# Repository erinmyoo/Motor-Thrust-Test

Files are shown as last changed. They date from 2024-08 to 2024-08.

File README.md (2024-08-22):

NSF REU: Collaborative Human-Robot Interaction for Robots in the Field at University of Nevada, Reno

For information about the full research project: [Paper](https://github.com/erinmyoo/Motor-Thrust-Test/blob/main/REU_Erin_Yoo.pdf)

# Motor-Thrust-Test
The goal of the Motor Thrust Test is to determine the reliability of the motors chosen for a solar-powered UAV called the Gannet. Wind Tunnel and Cyclic Marine Testing will evaluate the performace of the motor-propeller combination that is reported to produce 0.8 kg of thrust at a speed of 14 m/s and cruise power of 110 W.

## Test Stand Design
Completed Solidworks CAD Assembly and BOM is uploaded
* CAD Assembly is named ZBarStand

Manufacturing methods: horizontal bandsaw, mill, CNC mill (for Motor Mount)

Important Features:
* Motor Mount: Machined aluminum, cross mounting pattern to fit motors from 19 mm to 25 mm
* Single-Point Load Cell: withstand up to 10 kg of pressure
* Z-bar Configuration: accounts for the lip of the test tank, COG allows for the motor to fall back into the tank when disengaged
* Base Angle Brackets: bearings to allow the Z-bar to rotate, slots on top for hardstops
* Hardstops: two slots to press fit into Base Angle Brackets to contrain movement
* Pitot Tube: measures air speed and ground speed, not included in CAD



## Wind Tunnel Testing - Dynamic Thrust 
Dynamic thrust testing will conduct a Wind Tunnel Test using various motor and propeller combinations. The Test Stand will be strapped on top of the car while driving at the Gannet's cruise speed of 14 m/s. 

Status:
* Script finished
* Tested once
* Needs further data/testing to determine if motor efficiency is consistently calculated to be ~37%

## Cyclic Marine Testing - Static Thrust
Static thrust of the motor will be evaluated through Cyclic Marine Testing that simulates a multi-day mission at sea to validate corrosion mitigation. The motor will run continuously for 24 hours while the Test Stand dunks the motor in and out of the test tank filled with salt water.

Status:
* Script is mostly finished - issues with system receiving motor commands
* Testing needs to start

## Test Script
Python, ROS and MAVROS was used to automate testing and log data to a csv file.

Libraries used for setting up the Load Cell:
* [smbus2](https://pypi.org/project/smbus2/)
* [PyNAU7802](https://github.com/BrunoB81HK/PyNAU7802/tree/main)

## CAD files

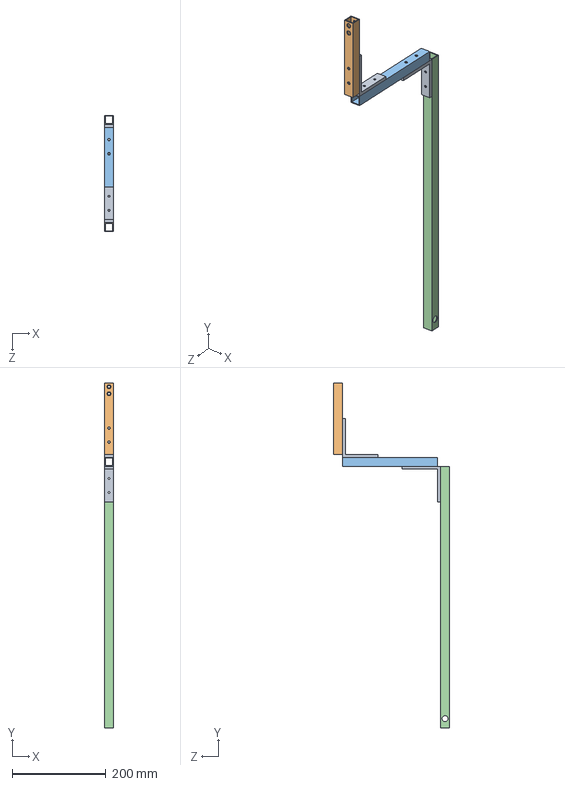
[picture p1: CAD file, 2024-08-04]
Test Stand CAD Files/ZBar.SLDASM
19.1 x 736.6 x 247.7 mm
Tube3
Tube2
Tube1
ZBarBracket x 2

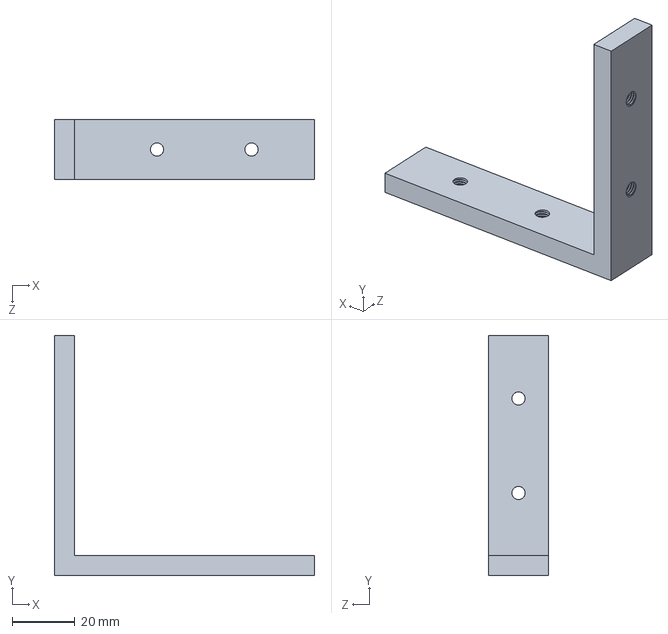
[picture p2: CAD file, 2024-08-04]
Test Stand CAD Files/ZBarBracket.SLDPRT
82.6 x 76.2 x 19.1 mm

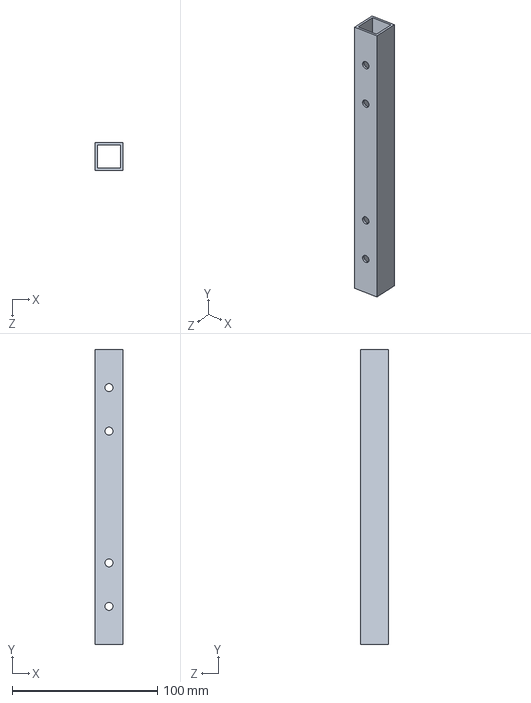
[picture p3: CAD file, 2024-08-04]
Test Stand CAD Files/Tube2.SLDPRT
19.1 x 203.2 x 19.1 mm

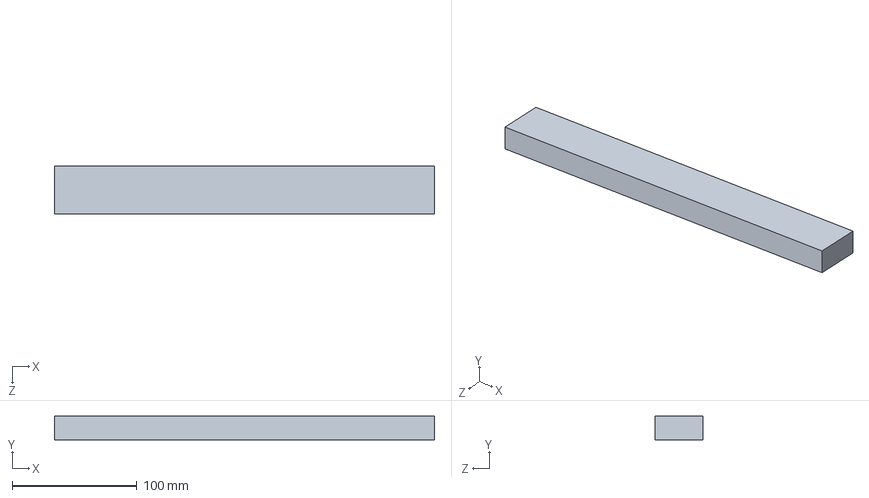
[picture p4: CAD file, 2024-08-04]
Test Stand CAD Files/WoodPlank_support.SLDPRT
304.8 x 19.1 x 38.1 mm

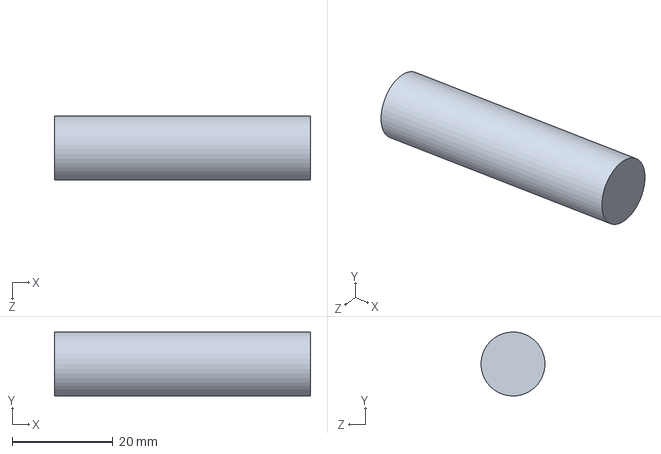
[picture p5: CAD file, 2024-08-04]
Test Stand CAD Files/Shaft.SLDPRT
50.8 x 12.7 x 12.7 mm

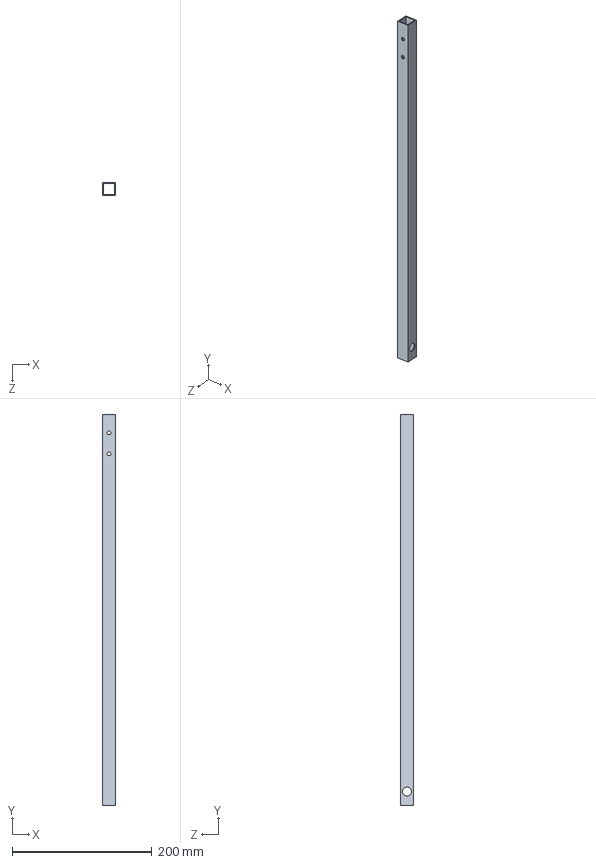
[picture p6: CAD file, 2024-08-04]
Test Stand CAD Files/Tube3.SLDPRT
19.1 x 558.8 x 19.1 mm

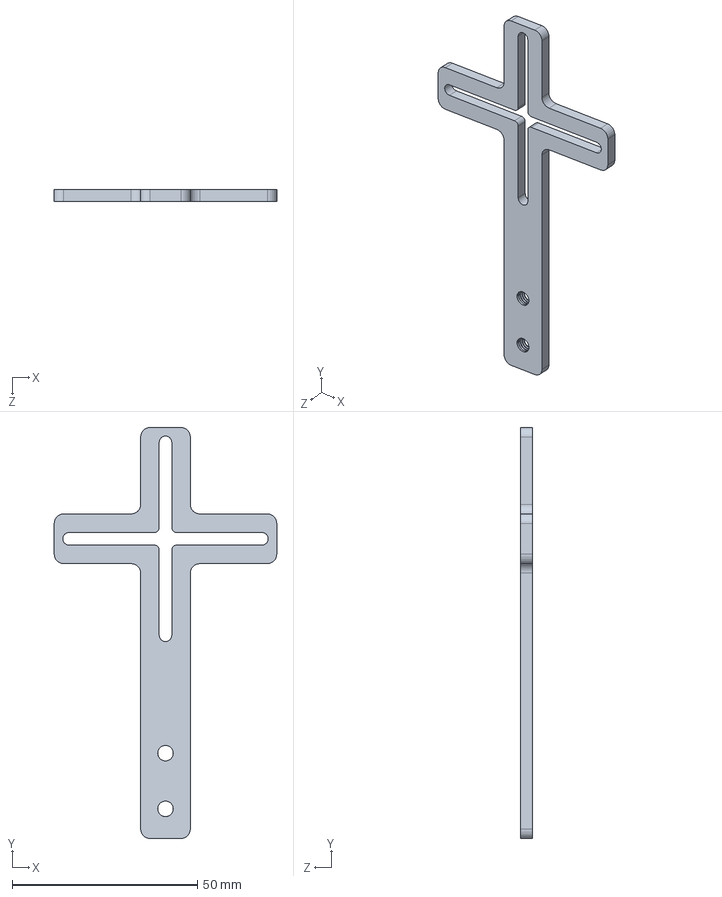
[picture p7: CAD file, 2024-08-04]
Test Stand CAD Files/0.125in_MotorMount.SLDPRT
60.0 x 110.8 x 3.18 mm

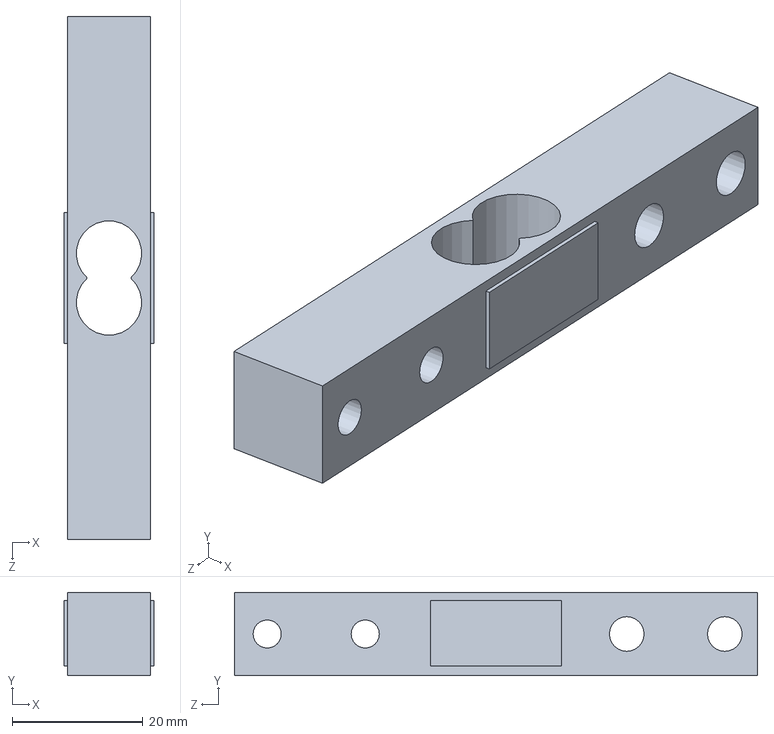
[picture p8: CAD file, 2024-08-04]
Test Stand CAD Files/TAL220 parallel beam load cell.SLDPRT
13.7 x 12.7 x 80.0 mm

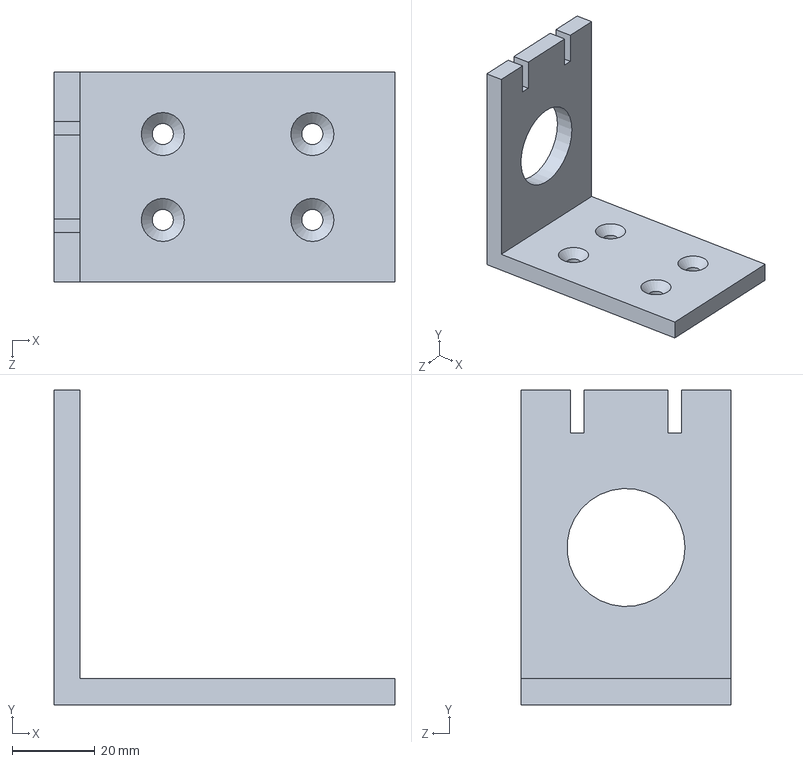
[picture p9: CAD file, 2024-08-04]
Test Stand CAD Files/L-bracket.SLDPRT
82.5 x 76.2 x 50.8 mm

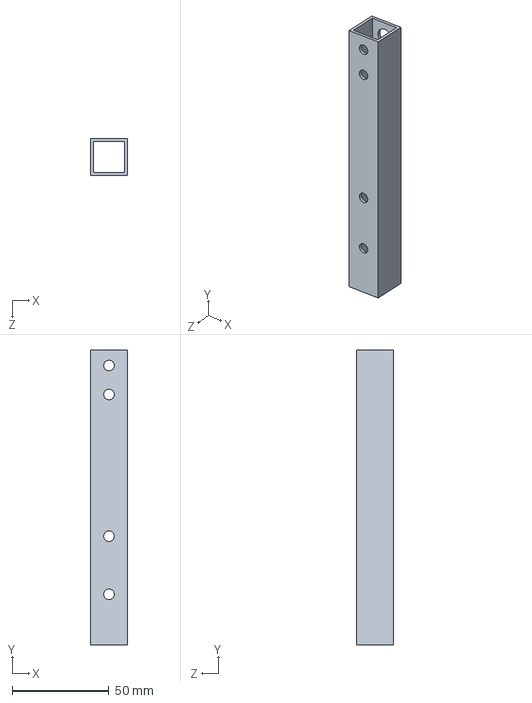
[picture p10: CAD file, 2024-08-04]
Test Stand CAD Files/Tube1.SLDPRT
19.1 x 152.4 x 19.1 mm

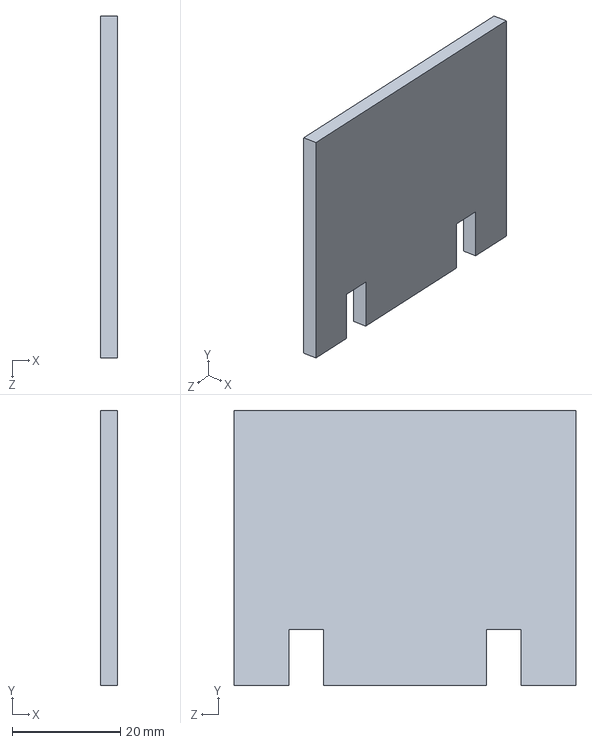
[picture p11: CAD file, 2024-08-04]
Test Stand CAD Files/Hardstop.SLDPRT
3.17 x 50.8 x 63.1 mm

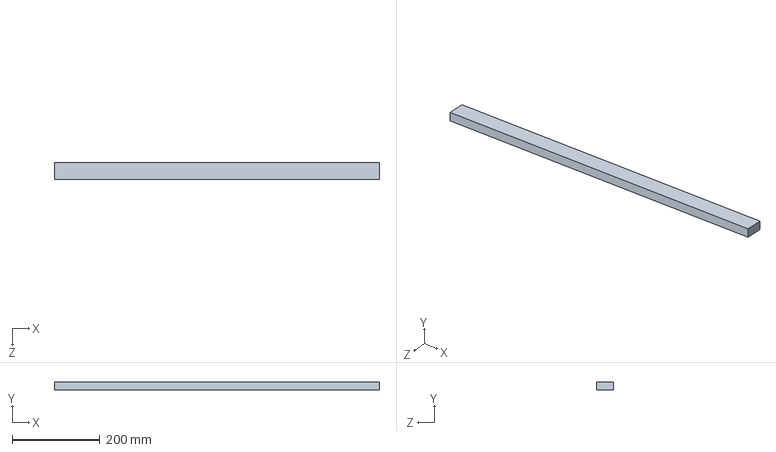
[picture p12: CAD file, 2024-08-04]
Test Stand CAD Files/WoodPlank.SLDPRT
740.0 x 19.1 x 38.1 mm

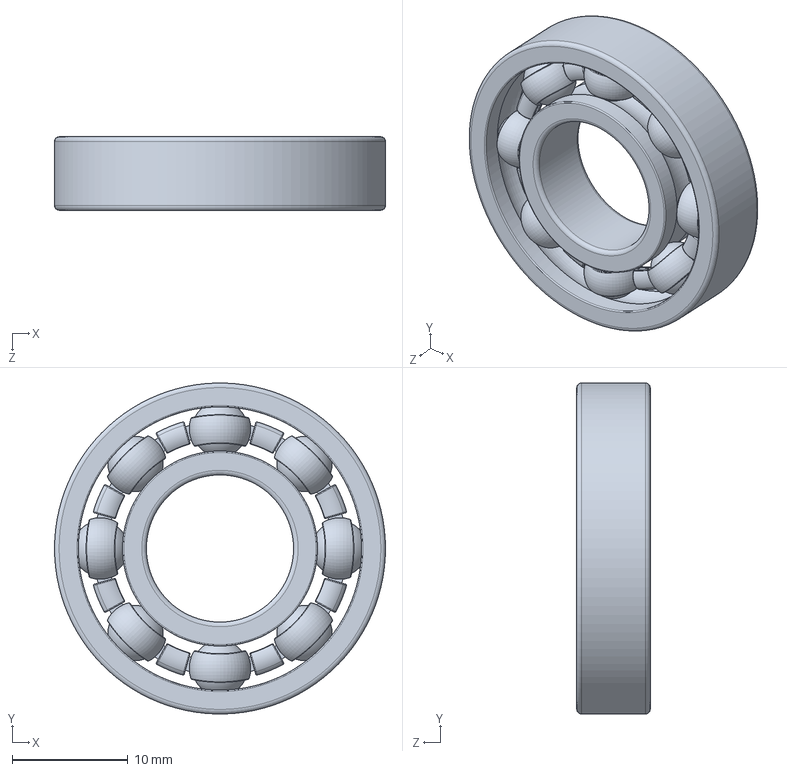
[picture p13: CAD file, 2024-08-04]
Test Stand CAD Files/60355K173_Ball Bearing.SLDPRT
28.6 x 28.6 x 6.35 mm

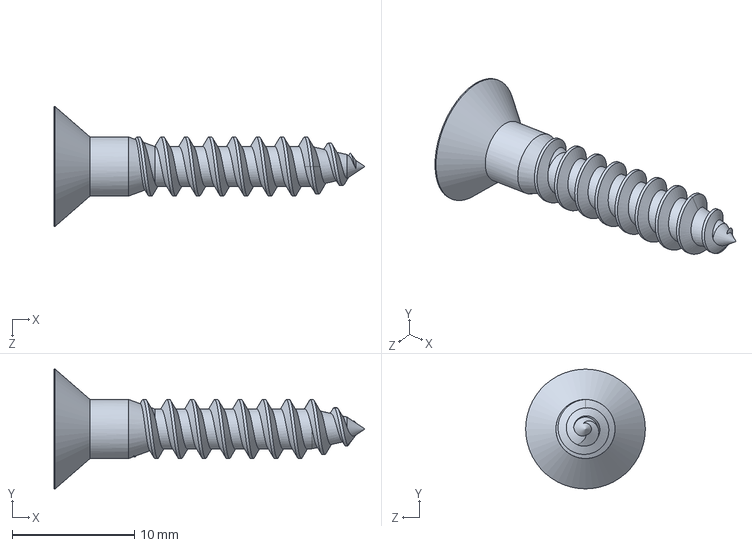
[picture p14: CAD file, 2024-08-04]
Test Stand CAD Files/90294A813_Phillips Flat Head Screws for Wood.SLDPRT
25.4 x 9.78 x 9.78 mm

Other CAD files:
Test Stand CAD Files/90819A112_Medium-Strength Steel Nylon-Insert Locknut.SLDPRT
Test Stand CAD Files/92290A771_Super-Corrosion-Resistant 316 Stainless Steel Socket Head Screw.SLDPRT
Test Stand CAD Files/92290A782_Super-Corrosion-Resistant 316 Stainless Steel Socket Head Screw.SLDPRT
Test Stand CAD Files/90819A111_Medium-Strength Steel Nylon-Insert Locknut.SLDPRT

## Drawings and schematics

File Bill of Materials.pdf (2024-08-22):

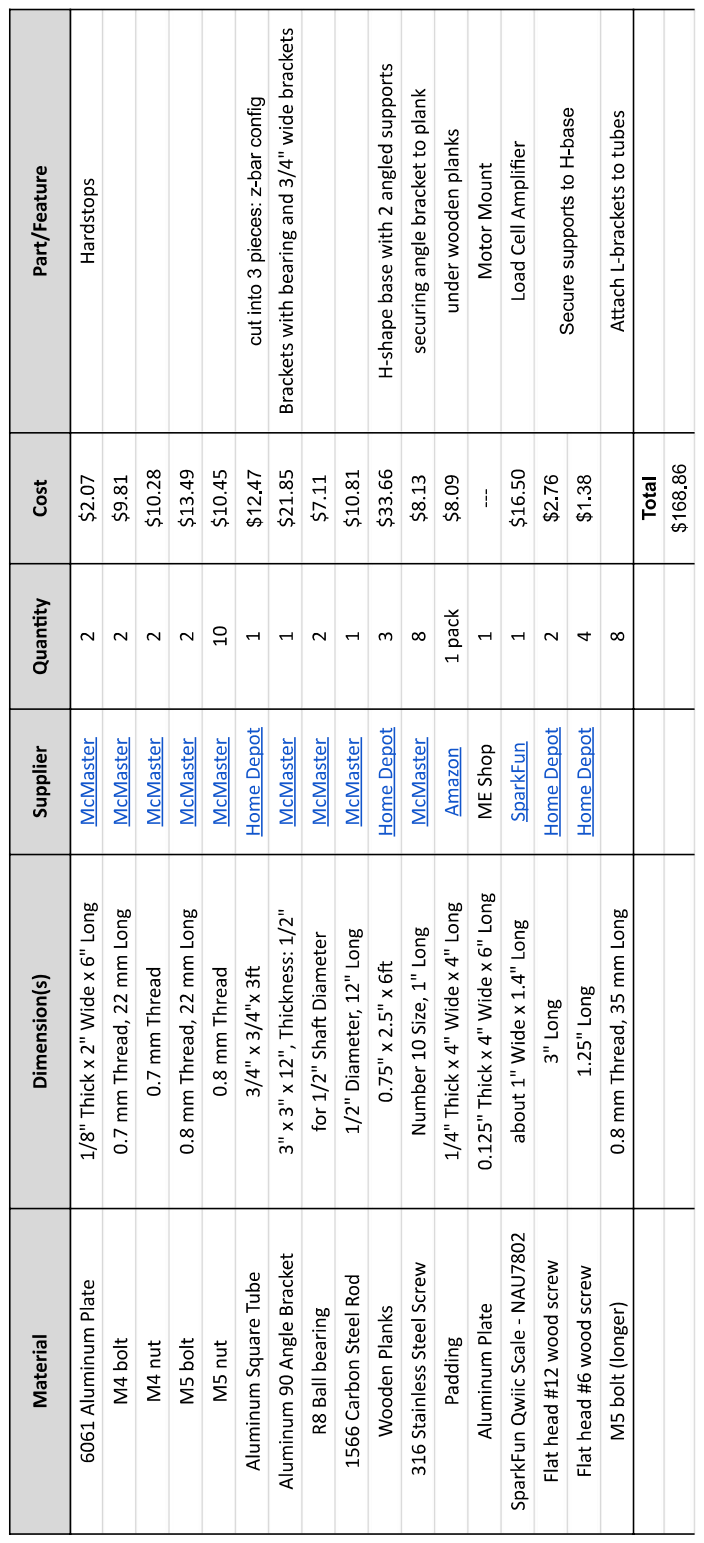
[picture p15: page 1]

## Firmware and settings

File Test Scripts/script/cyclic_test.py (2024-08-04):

#!/usr/bin/env python3
# Test Script for Cyclic Testing
import rospy
import time, csv
import load_cell
from mavros_msgs.srv import CommandBool, CommandLong
from mavros_msgs.msg import State
from sensor_msgs.msg import BatteryState
from pymavlink import mavutil

# Command Long 
def motor_output_cmd(motor_command, set_pwm):
    motor_command( # Parameters based on MAVROS
        0,
        mavutil.mavlink.MAV_CMD_DO_SET_SERVO, # command
        0,    # confirmation
        8,    # Servo number
        set_pwm, # PWM
        0, 0, 0, 0, 0
    )

thrust_gannet = None
voltage = None
current = None

def arming_state_callback(data):
    if data.armed:
        return True
    else:
        return False

def battery_callback(data):
    global voltage, current
    voltage = data.voltage
    current = data.current

def main():
    rospy.init_node("open_loop_test", anonymous = True)
    arming_state = rospy.Subscriber("/mavros/state", State, arming_state_callback)
    arming_proxy = rospy.ServiceProxy('/mavros/cmd/arming', CommandBool)
    battery_info = rospy.Subscriber("/mavros/battery", BatteryState, battery_callback)    
    motor_command = rospy.ServiceProxy('/mavros/cmd/command', CommandLong)

    load_cell # sets up load cell

    # log data to a file
    with open('data.csv', 'a') as file:
        writer = csv.writer(file)
        field = ['Time', 'Thrust from Gannet', 'Thrust from load cell', 'Voltage', 'Current']
        writer.writerow(field)

        one_day = 24*60*60
        current_time = time.time()

        while (not rospy.is_shutdown()) and (current_time <= one_day):
            if arming_state == False:
                arming_proxy(True)

            # PWM is set between 1000-2000
            max_motor = 2000
            motor_output = 1000 # starting
            increment = 0.05*max_motor
            decrement = 0.1*max_motor
            motor_output_cmd(motor_command, max_motor)  

            start = time.time()
            while (not rospy.is_shutdown()) and (time.time() - start) <= 60:
                if motor_output < max_motor:
                    motor_output += increment
                    motor_output_cmd(motor_command, motor_output) 
                    ramp_time = time.time()-start
                else:
                    #print('{0:0.4f}' .format(time.time()-start), loadcell.take_thrust(), voltage, current, motor_output, ramp_time)
                    writer.writerow(['{0:0.4f}' .format(time.time()-start), load_cell.take_thrust(), voltage, current, motor_output, ramp_time])
                time.sleep(0.2)

            end = time.time()
            while (not rospy.is_shutdown()) and (time.time() - end) <= 60:
                motor_output -= decrement
                motor_output_cmd(motor_command, motor_output) 
                if motor_output == 0:
                    break 
                time.sleep(0.2)
            
            time.sleep(5)
            arming_proxy(False)
            time.sleep(60)
            
            current_time = time.time()
        
        file.close()

if __name__ == '__main__':
    main()

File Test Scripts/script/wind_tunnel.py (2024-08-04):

#!/usr/bin/env python3
# Test Script for Wind Tunnel Testing

import rospy
import time, csv
import load_cell
from mavros_msgs.srv import CommandBool, CommandLong
from mavros_msgs.msg import Thrust, State, ESCTelemetry, VFR_HUD, RCIn, ESCTelemetryItem
from sensor_msgs.msg import BatteryState
from pymavlink import mavutil

# Command Long 
def motor_output_cmd(motor_command, set_pwm):
    motor_command( # Parameters based on MAVROS
        0,
        mavutil.mavlink.MAV_CMD_DO_SET_SERVO, # command
        0,    # confirmation
        8,    # Servo number
        set_pwm, # PWM
        0, 0, 0, 0, 0
    )

voltage = None
current = None
airspeed = None
groundspeed = None
esc_rmp = None
throttle = None

def arming_state_callback(data):
    if data.armed:
        return True
    else:
        return False

def battery_callback(data):
    global voltage, current
    voltage = data.voltage
    current = data.current

def esc_callback(data):
    global esc_rmp
    esc_rmp = data.esc_telemetry[8].rpm

def vfr_callback(data):
    global airspeed, groundspeed
    airspeed = data.airspeed
    groundspeed = data.groundspeed

def RC_callback(data):
    global throttle
    throttle = data.channels[2]

def main():
    rospy.init_node("wind_tunnel_test", anonymous = True)
    arming_state = rospy.Subscriber("/mavros/state", State, arming_state_callback)
    arming_proxy = rospy.ServiceProxy('/mavros/cmd/arming', CommandBool)
    rospy.Subscriber("/mavros/battery", BatteryState, battery_callback)    
    motor_command = rospy.ServiceProxy('/mavros/cmd/command', CommandLong)
    rospy.Subscriber("/mavros/esc_telemetry", ESCTelemetry, esc_callback)    
    rospy.Subscriber("/mavros/vfr_hud", VFR_HUD, vfr_callback)    
    rospy.Subscriber("/mavros/rc/in", RCIn, RC_callback)    


    if arming_state == False:
            arming_proxy(True)

    max_motor = 2000   
    motor_output_cmd(motor_command, max_motor)   

    load_cell # sets up load cell

    # log data to a file
    with open('data.csv', 'a') as file:
        writer = csv.writer(file)
        field = ['Time (s)', 'Thrust from load cell (kg)', 'Voltage (V)', 'Current (A)', 'Air Speed (m/s)', 'Ground Speed (m/s)', 'ESC RPM (1/min)', 'Throttle (PWM)']
        writer.writerow(field)
        
        start_time = time.time()
        while not rospy.is_shutdown():
            #print('{0:0.4f}' .format(time.time()-start_time), load_cell.take_thrust(), voltage, current, airspeed, groundspeed, esc_rmp, throttle)
            writer.writerow(['{0:0.4f}' .format(time.time()-start_time), load_cell.take_thrust(), voltage, current, airspeed, groundspeed, esc_rmp, throttle])
            time.sleep(0.1)        
        
        file.close()

if __name__ == '__main__':
    main()
